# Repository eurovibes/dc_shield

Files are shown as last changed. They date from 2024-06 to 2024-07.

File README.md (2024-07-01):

<!-- SPDX-FileCopyrightText: 2023 Benedikt Spranger <b.spranger@linutronix.de> -
->
<!-- SPDX-License-Identifier: CERN-OHL-S-2.0 -->


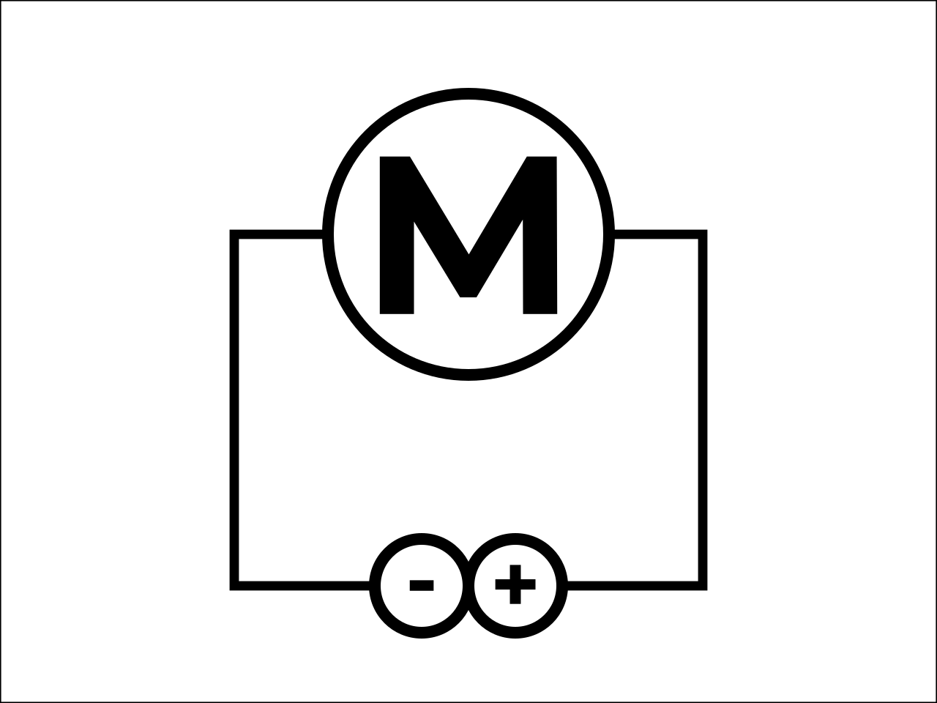
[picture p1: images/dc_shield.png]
dc_shield project logo


# dc_shield - A IFX9201 based Arduino Uno R3 motor shield

## License rules

dc_shield is provided under the terms of the CERN-OHL-S license
version 2 as provided in the LICENSES/CERN-OHL-S-2.0 file.

Instead of adding license boilerplates to the individual files,
dc_shield uses SPDX license identifiers, which are machine parseable
and considered legaly equivalent.

The SPDX license identifier in dc_shield shall be added at the first
possible line in a file which can contain a comment. This is normally the
first line except for scripts. Scripts require the #!PATH_TO_INTERPRETER tag
in the first line; place the SPDX identifier into the second line.

The SPDX license identifier is added in form of a comment.

## Copyright and License

> Copyright Benedikt Spranger 2023.
> This source describes Open Hardware and is licensed under the CERNOHL-S v2.
> You may redistribute and modify this source and make products using it
> under the terms of the CERN-OHL-S v2 (https://ohwr.org/cern ohl s v2.txt ).
> This source is distributed WITHOUT ANY EXPRESS OR IMPLIED WARRANTY, INCLUDING
> OF MERCHANTABILITY, SATISFACTORY QUALITY AND FITNESS FOR A PARTICULAR PURPOSE.
> Please see the CERN-OHL-S v2 for applicable conditions.
> Source location: https://github.com/eurovibes/dc_shield
> As per CERN-OHL-S v2 section 4, should You produce hardware based
> on this source, You must where practicable maintain the Source Location
> visible on the external case of the dc_shield or other products you
> make using this source.

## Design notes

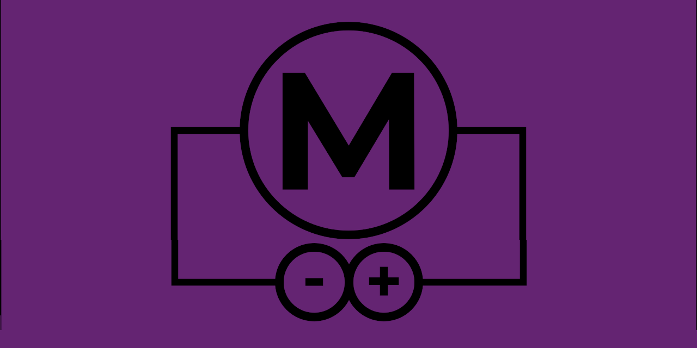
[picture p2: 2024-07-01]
images/dc_shield_media.png

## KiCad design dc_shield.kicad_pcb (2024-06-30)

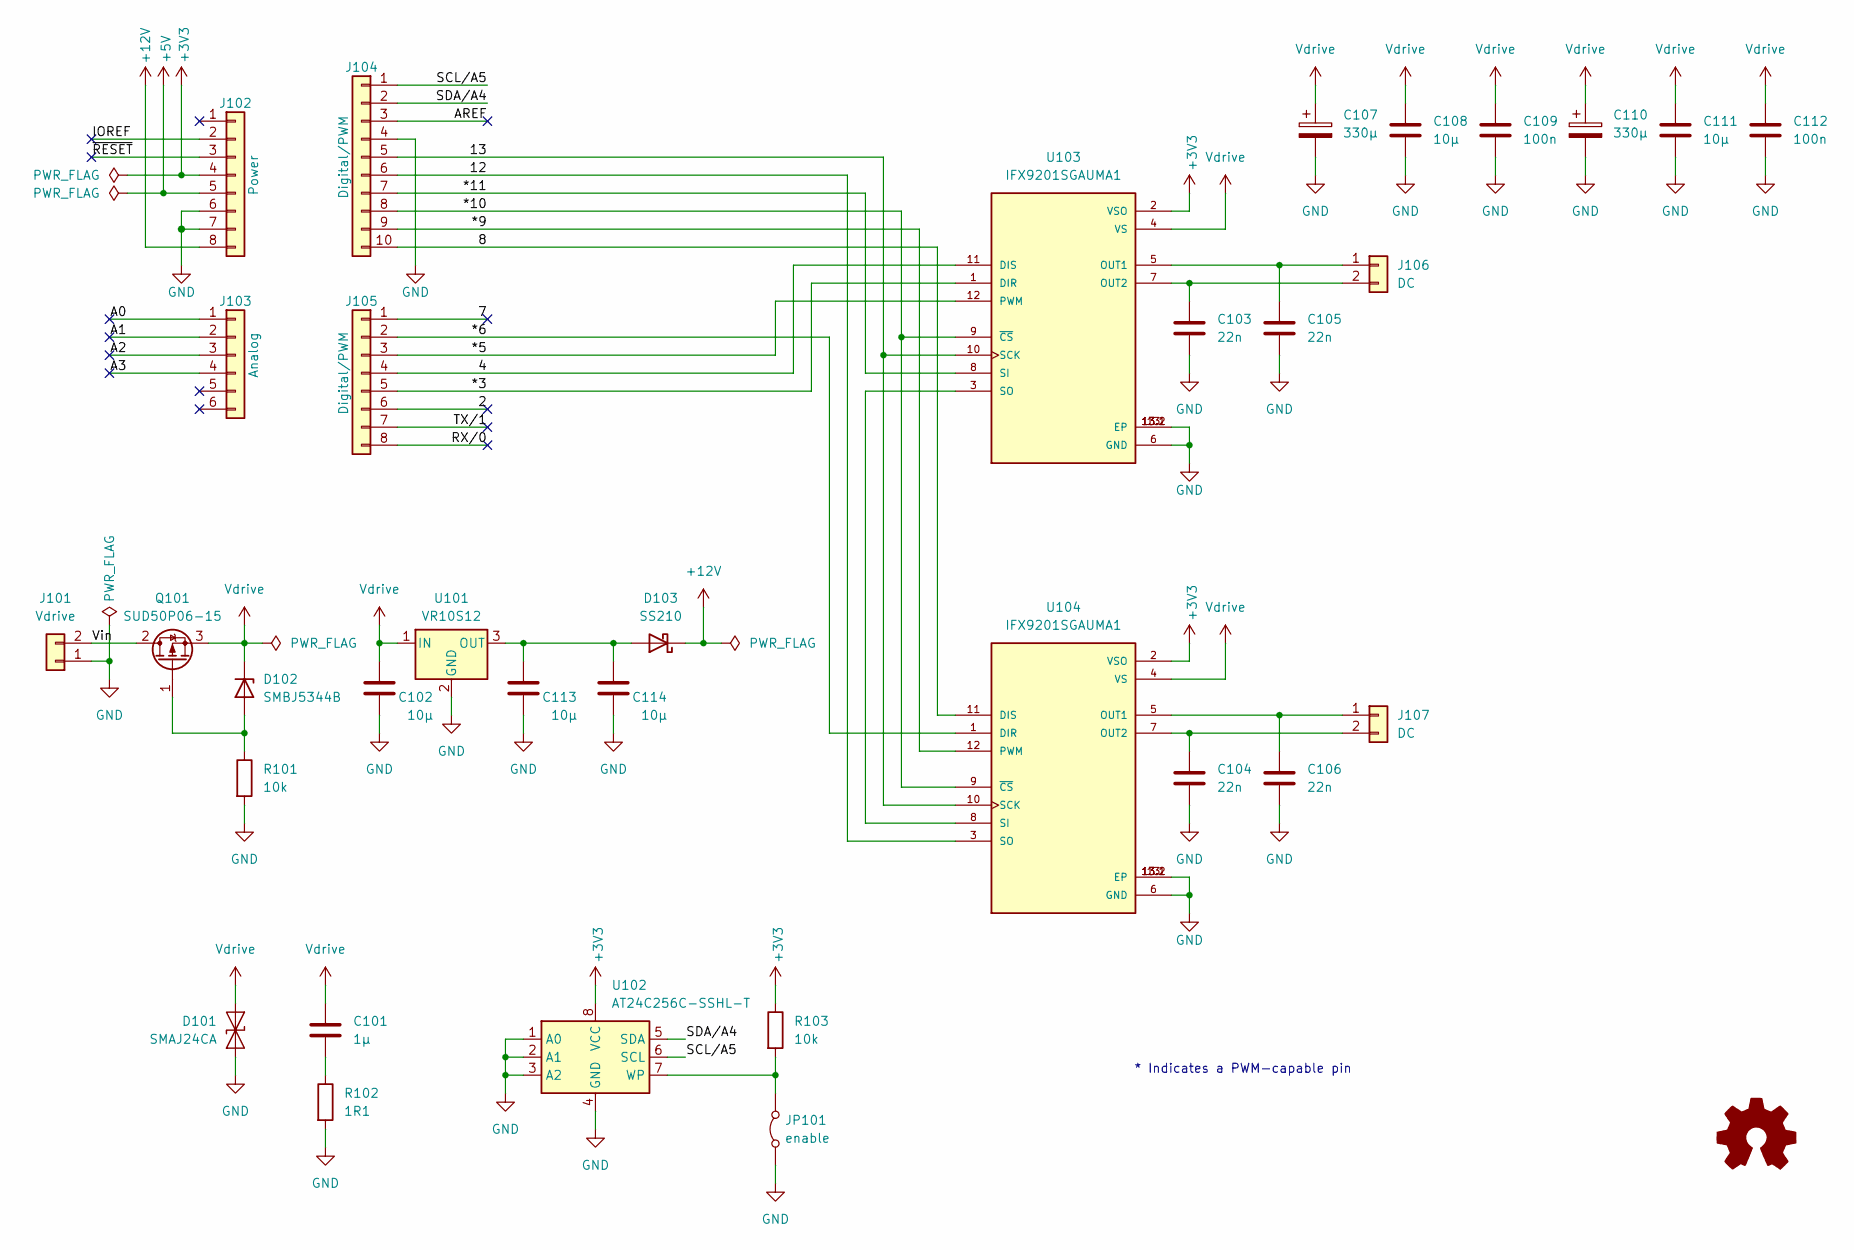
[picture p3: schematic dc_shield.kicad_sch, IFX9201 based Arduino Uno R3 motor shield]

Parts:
C101: 1µ; C_0603_1608Metric; mpn 0603F105M500NT; LCSC# C108343
C102, C108, C111, C113, C114: 10µ; C_1206_3216Metric; mpn C3216X5R1H106KT000N; LCSC# C329928
C103, C104, C105, C106: 22n; C_0603_1608Metric; mpn CC0603KRX7R9BB223; LCSC# C106222
C107, C110: 330µ; CP_Elec_10x10.5; mpn CS1H331M-CRG10; LCSC# C5162354
C109, C112: 100n; C_0603_1608Metric; mpn CL10B104KB8NNNC; LCSC# C1591
D101: SMAJ24CA; D_SMA; mpn SMAJ24CA; LCSC# C3001961
D102: SMBJ5344B; D_SMB; mpn SMBJ5344B; LCSC# C2903883
D103: SS210; D_SMA; mpn SS210; LCSC# C14996
J101: Vdrive; TerminalBlock_WAGO_236-402_1x02_P5.00mm_45Degree; mpn 236-402; digikey# 2946-236-402-ND
J102: Power; PinSocket_1x08_P2.54mm_Vertical; mpn PRT-11417; digikey# 1568-1413-ND
J103: Analog; PinSocket_1x06_P2.54mm_Vertical; mpn PRT-11417; digikey# 1568-1413-ND
J104: Digital/PWM; PinSocket_1x10_P2.54mm_Vertical; mpn PRT-11417; digikey# 1568-1413-ND
J105: Digital/PWM; PinSocket_1x08_P2.54mm_Vertical; mpn PRT-11417; digikey# 1568-1413-ND
J106, J107: DC; TerminalBlock_WAGO_236-402_1x02_P5.00mm_45Degree; mpn 236-402; digikey# 2946-236-402-ND
JP101: enable; SolderJumper-2_P1.3mm_Open_Pad1.0x1.5mm; mpn N/A
Q101: SUD50P06-15; TO-252-2; mpn SUD50P06-15-GE3; LCSC# C141584
R101, R103: 10k; R_0402_1005Metric; mpn AR02DTC1002; LCSC# C319934
R102: 1R1; R_1206_3216Metric; mpn WR12W1R10FTL; LCSC# C168518
U101: VR10S12; Converter_DCDC_RECOM_R-78E-0.5_THT; mpn VR10S12; digikey# 1470-VR10S12-ND
U102: AT24C256C-SSHL-T; SOIC-8_3.9x4.9mm_P1.27mm; mpn AT24C256C-SSHL-T; LCSC# C6482
U103, U104: IFX9201SGAUMA1; CONV_IFX9201SGAUMA1; mpn IFX9201SGAUMA1; LCSC# C112633

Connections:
+3V3: J102.4, R103.1, U102.8 (VCC), U103.2 (VSO), U104.2 (VSO)
+5V: J102.5
+12V: D103.1 (K), J102.8
/2: J105.6
/4: J105.4, U103.11 (DIS)
/7: J105.1
/8: J104.10, U104.11 (DIS)
/12: J104.6, U104.3 (SO)
/13: J104.5, U103.10 (SCK), U104.10 (SCK)
/*3: J105.5, U103.1 (DIR)
/*5: J105.3, U103.12 (PWM)
/*6: J105.2, U104.1 (DIR)
/*9: J104.9, U104.12 (PWM)
/*10: J104.8, U103.9 (~CS), U104.9 (~CS)
/*11: J104.7, U103.8 (SI)
/A0: J103.1
/A1: J103.2
/A2: J103.3
/A3: J103.4
/AREF: J104.3
/IOREF: J102.2
/RX/0: J105.8
/SCL/A5: J104.1, U102.6 (SCL)
/SDA/A4: J104.2, U102.5 (SDA)
/TX/1: J105.7
/Vin: J101.2, Q101.2 (D)
/~RESET: J102.3
GND: C102.2, C103.2, C104.2, C105.2, C106.2, C107.2, C108.2, C109.2, C110.2, C111.2, C112.2, C113.2, C114.2, D101.1 (A1), J101.1, J102.6, J102.7, J104.4, JP101.1 (A), R101.2, R102.2, U101.2 (GND), U102.1 (A0), U102.2 (A1), U102.3 (A2), U102.4 (GND), U103.6 (GND), U103.13 (EP), U103.13.1 (EP), U103.13.2 (EP), U104.6 (GND), U104.13 (EP), U104.13.1 (EP), U104.13.2 (EP)
unnamed: C101.2, R102.1
unnamed: D102.2 (A), Q101.1 (G), R101.1
unnamed: C113.1, C114.1, D103.2 (A), U101.3 (OUT)
unnamed: C105.1, J106.1, U103.5 (OUT1)
unnamed: C103.1, J106.2, U103.7 (OUT2)
unnamed: C106.1, J107.1, U104.5 (OUT1)
unnamed: C104.1, J107.2, U104.7 (OUT2)
unnamed: JP101.2 (B), R103.2, U102.7 (WP)
unnamed: U103.3 (SO), U104.8 (SI)
Vdrive: C101.1, C102.1, C107.1, C108.1, C109.1, C110.1, C111.1, C112.1, D101.2 (A2), D102.1 (K), Q101.3 (S), U101.1 (IN), U103.4 (VS), U104.4 (VS)

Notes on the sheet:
* Indicates a PWM-capable pin

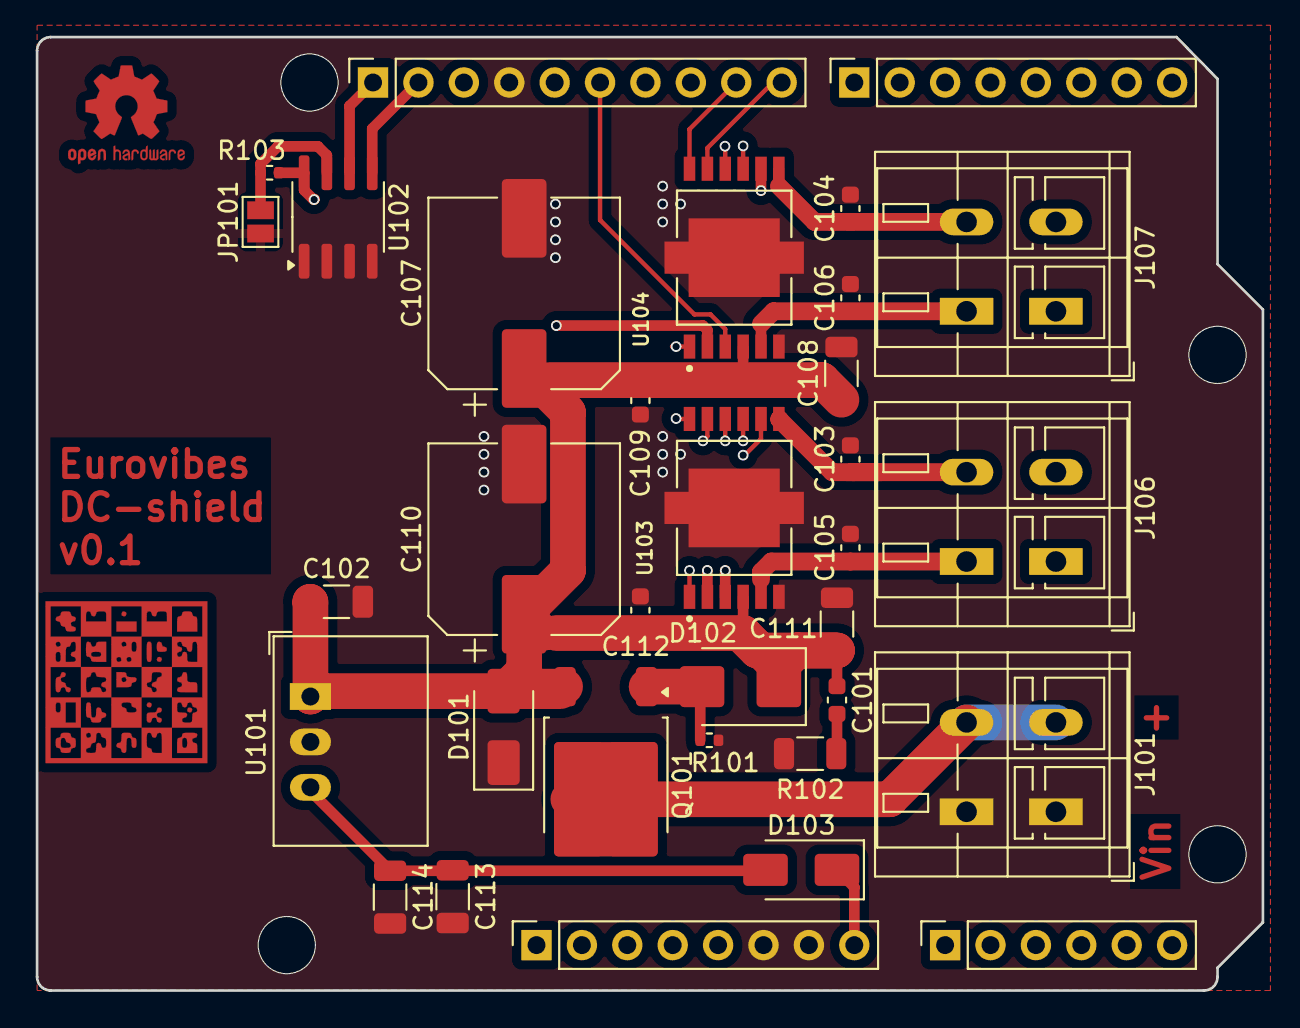
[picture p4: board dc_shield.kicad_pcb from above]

Board: 4 copper layers, 68.6 x 53.3 mm, 37 parts (0 on the bottom side), 26 nets.

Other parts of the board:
MH1, MH2, MH3, MH4: MountingHole_3.2mm

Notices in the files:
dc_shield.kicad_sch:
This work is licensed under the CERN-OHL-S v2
